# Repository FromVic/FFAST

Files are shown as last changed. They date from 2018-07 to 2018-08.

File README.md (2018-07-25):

# FFAST

## Introduction

The FFAST vehicle is a 1:10 scale RC car functioning as a test platform for testing dynamic motion planning and control algorithms. This repository contains the software developed throughout the project, including the source codes in the vehicle responsible for autonomous driving and executing maneuvers such as drifting and obstacle avoidance.

## Functionalities

The rear-wheel drive front steering vehicle is capable of driving with speed of up to 6 m/s forward and 3 m/s backwards and achieving steering angles of 30 degrees on either side. It achieves localization reasonably well using data from the Hall effect sensors on the motor as odometry, IMU, LIDAR and the camera on the Jetson developer kit with optic flow. It can be teleoperated or controlled by a software giving it navigation commands. An RF receiver on the vehicle stops vehicle operation when the remote transmitter is pressed, acting as an emergency kill switch.

## Organization

The repository is divided into several subfolders:
- doc  
Directory for instructions for developing the RC car platform and the detailed documentation of the project
- catkin_ws  
Catkin workspace containing the ROS packages that control the vehicle
- matlab_simulator  
MATLAB scripts for simulation of vehicle dynamics and execution of the maneuvers in simulation

## Getting Started

The [setup instructions](doc/setup_instructions.md) will get you a copy of the project up and running on your local machine for development and testing purposes. It has been developed for Linux, and no cross-compatibility effort has been made.

## Running the tests
Refer to the [test runs](doc/test_runs.md) for the commands to run the tests.

## Authors

* **Jordan Ford** - [jsford](https://github.com/jsford)
* **Emily Yunan** - [emilyfy](https://github.com/emilyfy)
* **Shihao Xu** - [FromVic](https://github.com/FromVic)

See also the list of [contributors](https://github.com/jsford/FFAST/contributors) who participated in this project.

## License

MIT License  
Copyright (C) 2017 Jordan Ford  
The Robotics Institute, Carnegie Mellon University

Permission is hereby granted, free of charge, to any person obtaining a copy of this software and associated documentation files (the "Software"), to deal in the Software without restriction, including without limitation the rights to use, copy, modify, merge, publish, distribute, sublicense, and/or sell copies of the Software, and to permit persons to whom the Software is furnished to do so, subject to the following conditions: The above copyright notice and this permission notice shall be included in all copies or substantial portions of the Software.

THE SOFTWARE IS PROVIDED "AS IS", WITHOUT WARRANTY OF ANY KIND, EXPRESS OR IMPLIED, INCLUDING BUT NOT LIMITED TO THE WARRANTIES OF MERCHANTABILITY, FITNESS FOR A PARTICULAR PURPOSE AND NONINFRINGEMENT. IN NO EVENT SHALL THE AUTHORS OR COPYRIGHT HOLDERS BE LIABLE FOR ANY CLAIM, DAMAGES OR OTHER LIABILITY, WHETHER IN AN ACTION OF CONTRACT, TORT OR OTHERWISE, ARISING FROM, OUT OF OR IN CONNECTION WITH THE SOFTWARE OR THE USE OR OTHER DEALINGS IN THE SOFTWARE.

## Acknowledgments

* Carnegie Mellon University 
* General Motors Research and Development

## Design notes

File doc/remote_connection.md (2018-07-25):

# Setting up local computer and vehicle remote connections
Other than sharing ROS master, the other steps here are optional but help in speeding up the setup process before test runs. Getting a passwordless sudo is necessary to get the emergency remote kill switch to work. Without a passwordless sudo, the jetson_gpio package will not be able to be run by the ROS server.

## Sharing ROS master
The car and a local computer have to share a common ROS master to run the tests. To do this, they must first be connected to the same network. Then, check the assigned IP on both computers by:
```bash
$ hostname -I
```
Assuming the local computer IP is 10.42.0.1 and the Jetson 10.42.0.2, on the local computer, in every terminal before running the ROS commands run these first
```bash
$ export ROS_MASTER_URI=http://10.42.0.2:11311
$ export ROS_IP=10.42.0.1
```
You can put these lines inside ~/.bashrc to set the ROS master by default. To run your own master, simply reverse the changes:
```bash 
$ export ROS_MASTER_URI=http://localhost:11311
$ unset ROS_IP
```

## Getting passwordless sudo
In the jetson, run the command
```bash
$ sudo visudo
```
On the last line, add the following:
```
username ALL = (ALL) NOPASSWD: ALL
```
replacing username with your user name.  
Note: it is important to use visudo to edit the file instead of manually editing it with other editors as an invalid file will lead to loss of access to sudo privileges.

## Synchronizing time across machines
If the system time in the different machines are not synchronized, the timestamp on ROS messages will differ and this may cause problems. To synchronize the system time, install Chrony on both computers:
```bash
$ sudo apt-get install ntpdate chrony
```
Edit the configuration file `/etc/chrony/chrony.conf` and add the following:  
On the local computer,
```
local stratum 8
allow jetson_ip
```
replacing car_ip with the IP address of the jetson.  
On the Jetson,
```
server local_ip iburst
```
replacing local_ip with the IP address of the local computer.

## Setting up static IP addresses
If a Wi-Fi adapter or router is used specifically for the connection between the local computer and remote RC car, static IP addresses can be assigned to both computers.

Using a Wi-Fi adapter (suppose the static IP to be assigned to the car is 10.42.0.2):
1. Connect the USB adapter to the local computer
2. Create a new Wi-Fi network , choosing the corresponding Wi-Fi adapter.
3. On the IPv4 settings, select the dropdown for Method to be Shared to other computers;In the Wi-Fi tab set Mode to 'Ad-hoc'         and Band to 'B/G (2.4 GHz)'.
4. On the Jetson, connect to the created Wi-Fi network.
5. Edit the network connection such that:  
   In the general tab both 'Automatically connect to this network when it is available' and 'All users may connect to this network' are checked  
   In the Wi-Fi tab set Mode to 'Ad-hoc' and Band to 'B/G (2.4 GHz)'
   In the IPv4 Settings tab the Method is set to Manual and add an address with  
   Address: 10.42.0.2  
   Netmask: 24  
   Gateway: 10.42.0.1 (IP of host)  
   DNS Servers: 8.8.8.8, 8.8.4.4
6. Disconnect and connect to the network again.

## Setup SSH shortcut
To avoid having to type in `ssh username@hostname` or `ssh username@hostip` everytime to access the remote terminal, one can setup an SSH config file to to create a shortcut for SSH to the host. (Instructions obtained from [here](http://nerderati.com/2011/03/17/simplify-your-life-with-an-ssh-config-file/)).
```bash
$ nano ~/.ssh/config
```
Enter the following:
```
Host shortcutname
HostName hostname
Port portnumber
User username
```
with the corresponding shortcut name, host name, port number and username. The default port number is 22.  
Then,
```bash
$ cd /etc/bash_completion.d/
$ sudo nano ssh
```
Copy and paste the following:
```
_ssh() 
{
    local cur prev opts
    COMPREPLY=()
    cur="${COMP_WORDS[COMP_CWORD]}"
    prev="${COMP_WORDS[COMP_CWORD-1]}"
    opts=$(grep '^Host' ~/.ssh/config | grep -v '[?*]' | cut -d ' ' -f 2-)

    COMPREPLY=( $(compgen -W "$opts" -- ${cur}) )
    return 0
}
complete -F _ssh ssh
```
From here onwards, the command `ssh shortcutname` will be equivalent to entering `ssh username@hostname -p portnumber`.

## Setting RSA key
Another inconvenience when accessing remote terminal is the need to enter the password everytime. However, by setting up the RSA key one can eliminate the need to do so. While connected to the same network, on the local computer:
```bash
$ ssh-keygen
  press enter or type your preferred file name for storing the key  
  press enter or type a password (this is a password to bet set on the stored key, not the user account password)  
  press enter again or type the same password  
$ chmod 755 ~/.ssh
$ ssh-copy-id -i id_rsa user@hostname (or change id_rsa to the filename you entered)
$ ssh -oHostKeyAlgorithms='ssh-rsa' user@hostname (if it fails, change ssh-rsa to the type shown in ~/.ssh/known_hosts)
$ chmod 600 ~/.ssh/authorized_keys
$ exit exit
$ ssh-agent bash
$ ssh-add ~/.ssh/id_rsa (or change id_rsa to the filename you entered)
$ exit
```
This needs to be done only the first time you use SSH to access the Jetson terminal. After this you can simply use the `ssh user@hostname` command

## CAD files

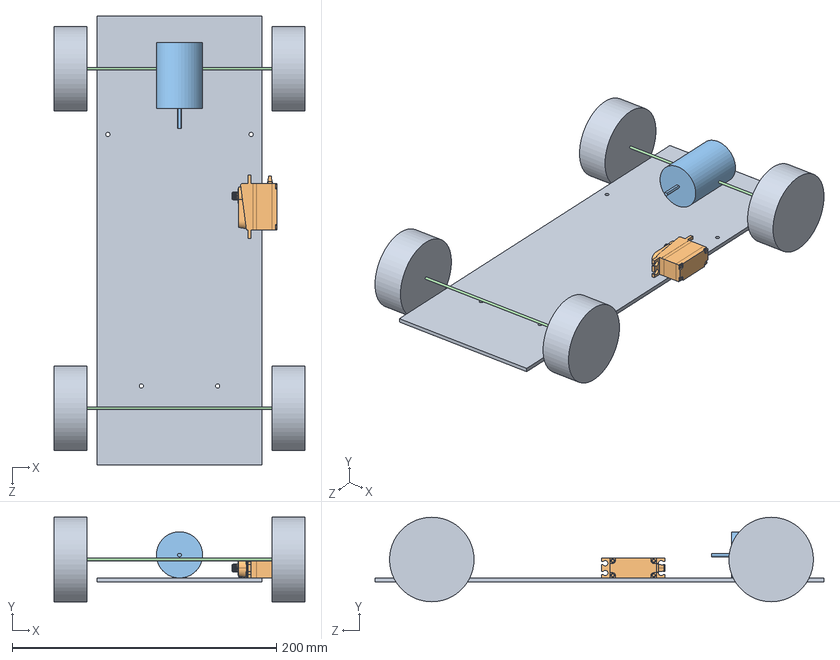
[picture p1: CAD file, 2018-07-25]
doc/CAD files/chassis with drivetrain.SLDASM
190.0 x 64.0 x 340.0 mm
chassis
Savox
motor
axle x 2

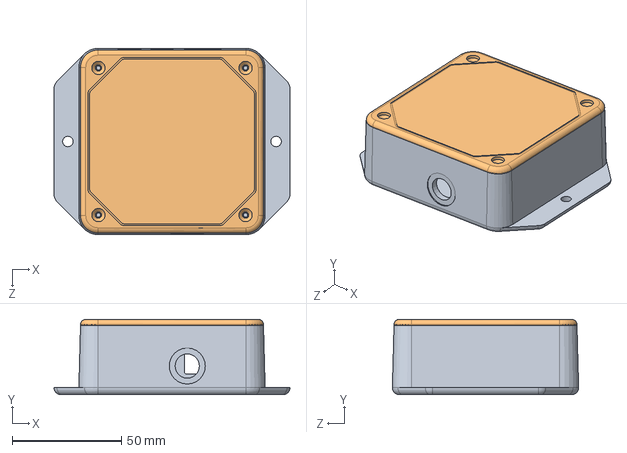
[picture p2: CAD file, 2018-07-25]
doc/CAD files/velodyne interface box.SLDASM
108.0 x 34.5 x 85.2 mm
50-6001a FAB ENCLOSURE
50-6002a LID ENCLOSURE

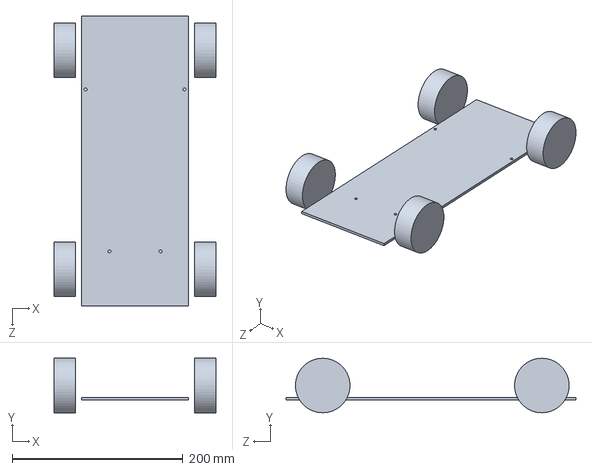
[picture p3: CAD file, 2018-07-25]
doc/CAD files/chassis.SLDPRT
190.0 x 64.0 x 340.0 mm

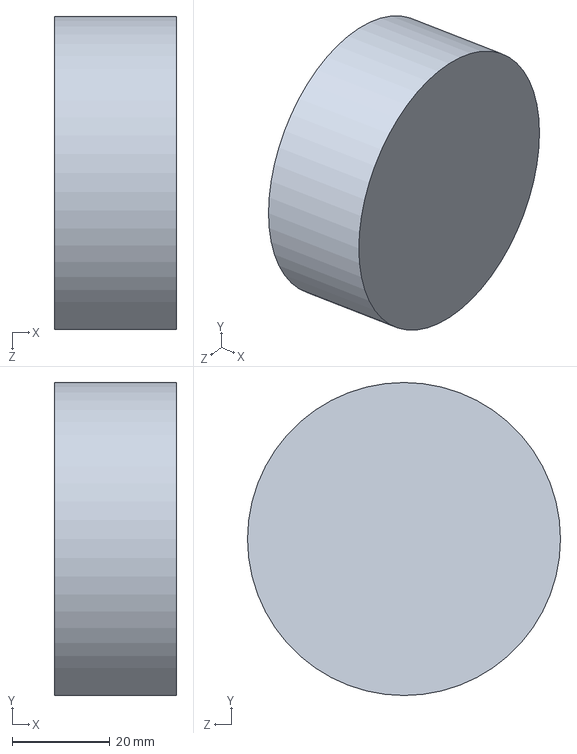
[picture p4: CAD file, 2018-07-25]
doc/CAD files/wheel.SLDPRT
25.0 x 64.0 x 64.0 mm

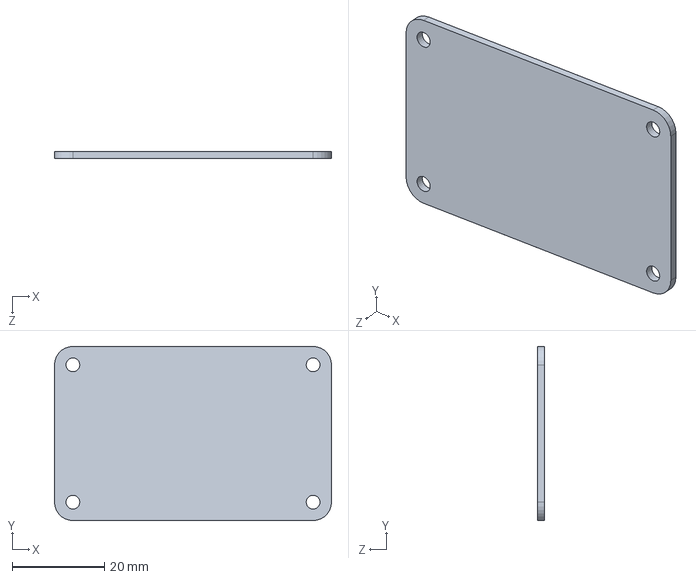
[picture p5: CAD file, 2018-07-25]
doc/CAD files/Vreg.SLDPRT
60.2 x 37.8 x 1.50 mm

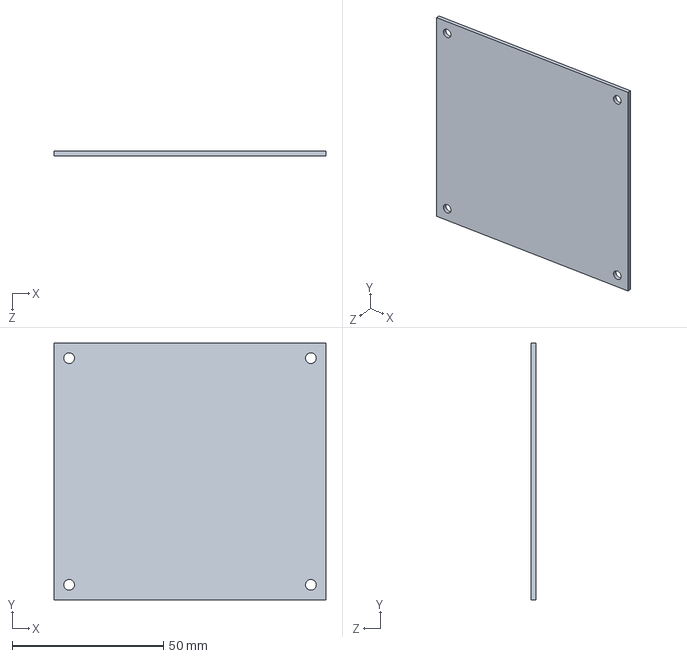
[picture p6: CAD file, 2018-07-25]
doc/CAD files/power dist board.SLDPRT
90.0 x 85.0 x 1.50 mm

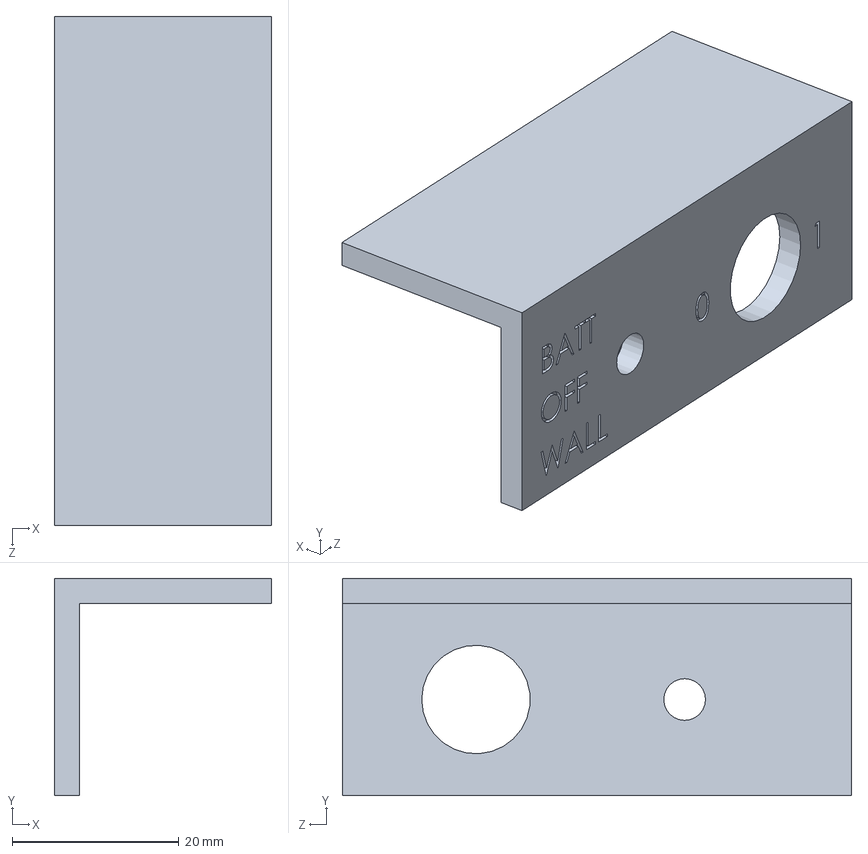
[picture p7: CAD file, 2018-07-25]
doc/CAD files/switch mount.SLDPRT
26.0 x 26.0 x 61.0 mm

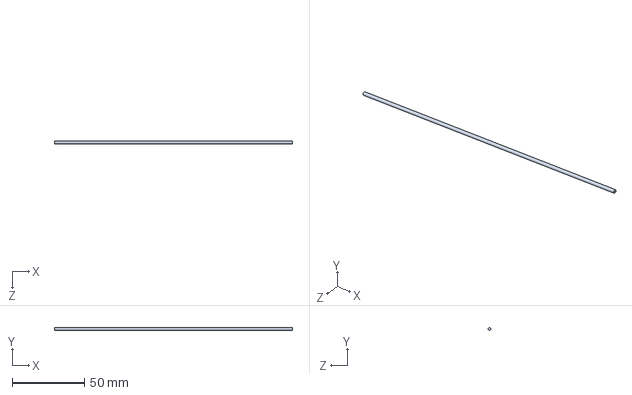
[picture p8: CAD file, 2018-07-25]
doc/CAD files/axle.SLDPRT
165.0 x 2.00 x 2.00 mm

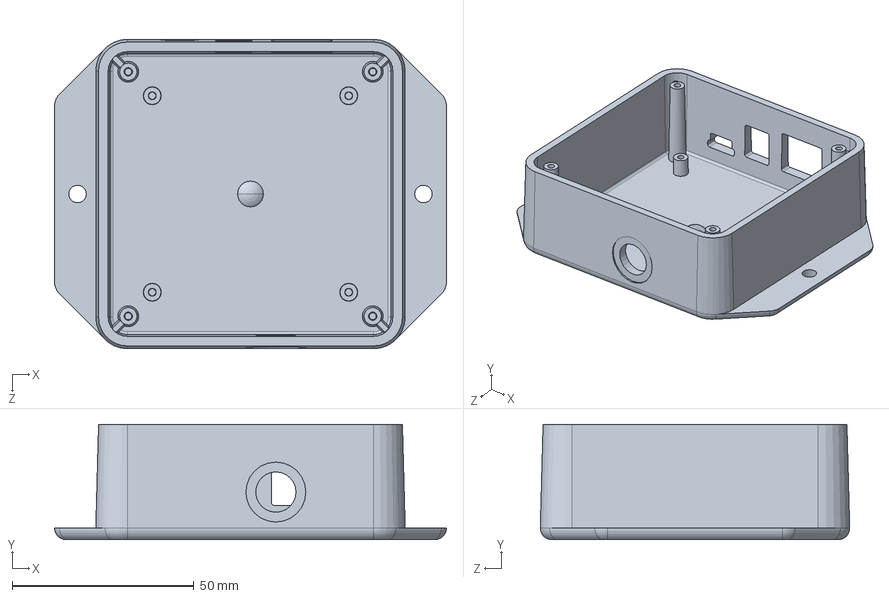
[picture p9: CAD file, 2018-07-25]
doc/CAD files/50-6001a FAB ENCLOSURE.SLDPRT
108.0 x 31.8 x 85.2 mm

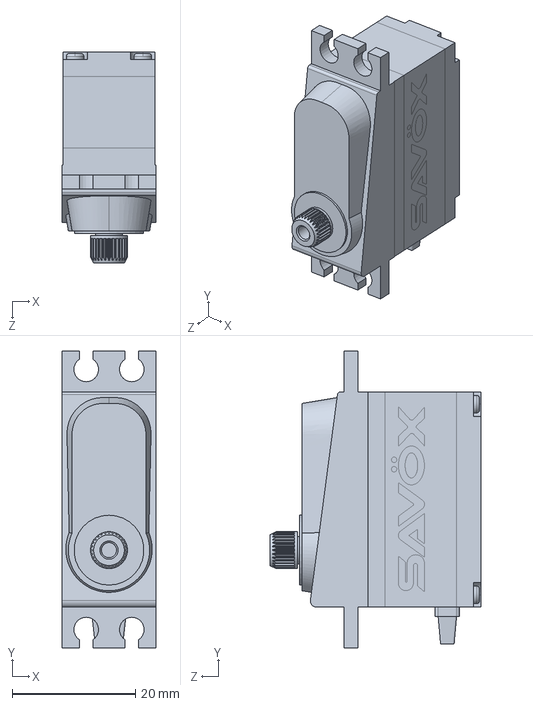
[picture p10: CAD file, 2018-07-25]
doc/CAD files/Savox.SLDPRT
15.2 x 48.2 x 34.3 mm

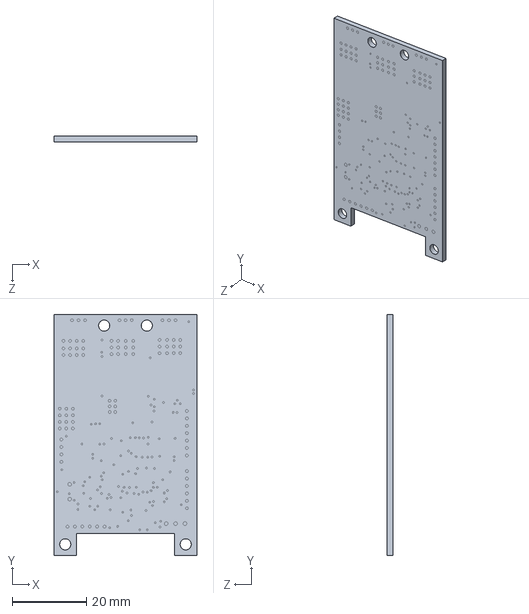
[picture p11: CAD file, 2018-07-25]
doc/CAD files/vesc.SLDPRT
38.5 x 65.0 x 1.58 mm

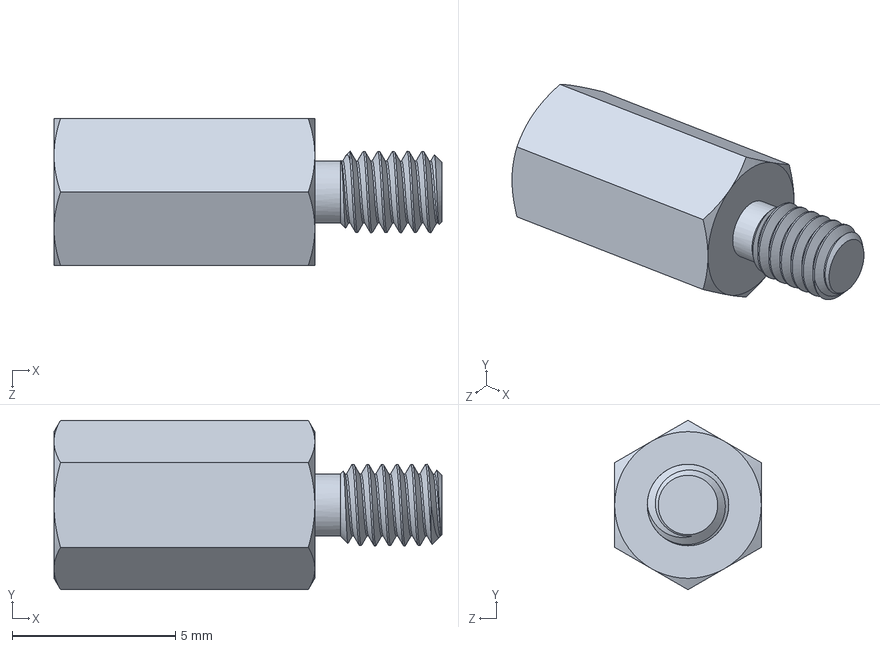
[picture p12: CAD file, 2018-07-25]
doc/CAD files/M2.5 8mm Male-Fem Standoff.SLDPRT
11.9 x 5.20 x 4.50 mm

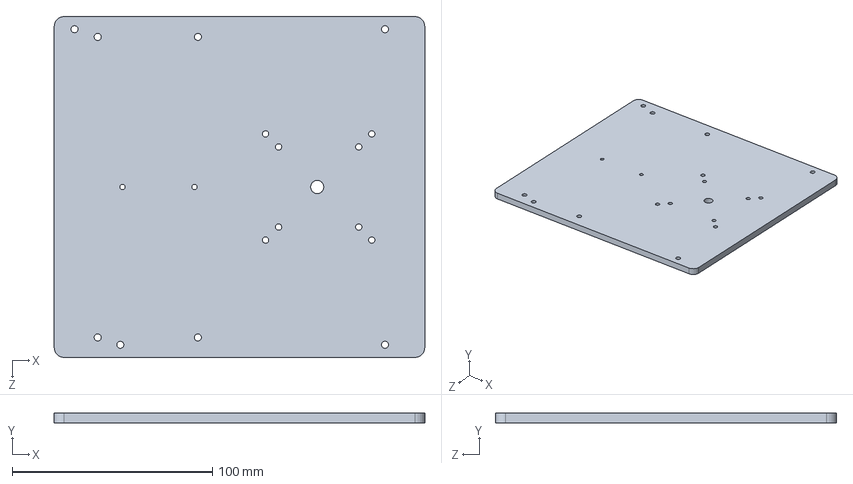
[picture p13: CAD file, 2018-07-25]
doc/CAD files/top plate.SLDPRT
185.0 x 4.76 x 170.2 mm

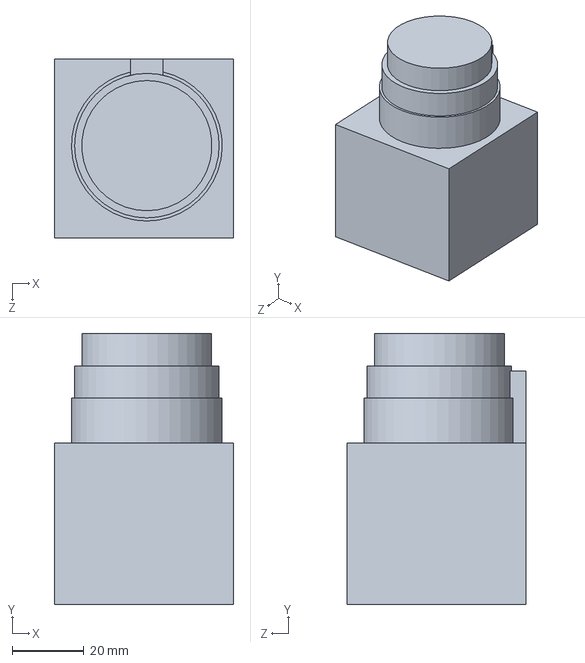
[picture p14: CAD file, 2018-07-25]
doc/CAD files/Hokuyo URG-04LX-UG01.SLDPRT
50.0 x 75.5 x 50.0 mm

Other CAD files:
doc/CAD files/6-32 2.5in Fem Standoff.SLDPRT
doc/CAD files/battery.SLDPRT
doc/CAD files/motor.SLDPRT
doc/CAD files/bottom plate.SLDPRT
doc/CAD files/50-6002a LID ENCLOSURE.SLDPRT
doc/CAD files/6-32 .25in Fem Standoff.SLDPRT
doc/CAD files/6-32 1in Male-Fem Standoff.SLDPRT
doc/CAD files/91115a134_18-8 ss fem thrded hex standoff.SLDPRT
doc/CAD files/91780A123_ALUM FEM THRDED HEX STANDOFF.SLDPRT
doc/CAD files/91780A133_ALUM FEM THRDED HEX STANDOFF.SLDPRT
doc/CAD files/93505A440_ALUM MALE-FEM THRDED HEX STANDOFF.SLDPRT
doc/CAD files/95783A019_NYLON 6-6 MALE-FEM THRDED HEX STANDOFF.SLDPRT
doc/CAD files/IMU.SLDPRT
doc/CAD files/Top cover.SLDPRT
doc/CAD files/big toggle switch.SLDPRT
doc/CAD files/protoboard.SLDPRT
doc/CAD files/small toggle switch.SLDPRT
doc/CAD files/usb hub.SLDPRT
doc/CAD files/velodyne lidar.SLDPRT
doc/dxf files/Top cover.DXF
doc/dxf files/top plate.DXF

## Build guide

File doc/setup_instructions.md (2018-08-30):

# Setup Instructions

## Parts List
| Component | Manufacturer & Model no. |
| ---|---|
| RC car chassis & drivetrain | MST FXX-D |
| Sensored BLDC motor | MST XBLS 601012 |
| Pinion gear | Boom racing 48P 19T |
| Servo motor | Savox SAVSB2274SG |
| Battery | Multistar 3S 11.1V 5200mAh |
| Single-board computer | Nvidia Jetson TX2 |
| IMU | Variense VMU931 |
| LIDAR | Hokuyo URG-04LX-UG01 |
| ESC | VESC 4.12 |

Other parts required include:
- acrylic plates
- switches
- gamepad controller
- USB hub
- USB to micro USB (x1) and USB to mini USB (x2) cables
- USB Wi-Fi adapter (optional)
- Wireless switch transmitter and receiver (for emergency remote kill switch, optional)
- PCB and components
- fasteners and standoffs
- wires and connectors

Refer to the [bill of materials](bill\ of\ materials.xlsx) for the complete list and websites the parts were sourced from in our project.

## Steps
1. Laser cut the acrylic plates with the DXF files in doc folder.
2. Manufacture the PCB with the eagle and gerber files.
3. Setup the electrical connections according to the [circuit diagram](circuit_diagram.pdf).
4. Load the firmware into the VESC and calibrate its settings (instructions [here](vesc_setup.md)).
5. Assemble the car according to the 3D mechanical design of the vehicle from [here](FFAST_Assem.SLDASM).
6. [Install ROS](http://wiki.ros.org/kinetic/Installation/Ubuntu) and all other [package dependencies](dependencies.md) on the Jetson TX2.(Please make sure the ROS verison installed to be ROS kinetic, otherwise there might be some compatibility problems)
7. Set the udev rules on the Jetson (for the VESC, IMU and LIDAR) and the local computer (for the controller). Refer to the [rules file](99-usb-serial.rules) and use the same symbolic links, changing the values accordingly. (Joystick settings may vary due to different types of controllers, please check values)
8. Have a local computer with ROS and the same packages installed to remotely control the car.
9. Setup the network connections between the local computer and the car (instructions [here](remote_connection.md)).
10. The vehicle is now ready for [test runs](test_runs.md).

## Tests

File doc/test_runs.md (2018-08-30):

# Test Runs
To power up the car, plug battery into voltage input plug on the power distribution board, and press the VESC switch button beside it. Once the blue light on VESC is turned on, press power button of the Jestson then the whole system will be turned on.

After powering up the Jetson and the VESC with the on-board battery and setting up the necessary remote network connections, the car is ready for running.

## Fundamental launches
```bash
$ roslaunch hardware hardware.launch
```
This starts all the hardware operations, including the VESC, IMU, LIDAR, camera, the corresponding static transforms broadcaster and the emergency kill switch listener on the GPIO. At this point, only odometry data and transform is published.  
The launch arguments are:
- predict_slip  
  Set to true to predict wheel slip. Displacement is underestimated during acceleration and high speed and overestimated during deceleration or braking.
- fuse_odom  
  Set to true to fuse the IMU data with motor sensors data before publishing in odom frame. The yaw will then always be obtained from the IMU.
- odom_tf  
  Set to true to broadcast odom to base_link transform.
```bash
$ roslaunch localization localization.launch
```
This starts the localization process, including scan matching, optic flow calculation, particle filter localization within the map and EKF that fuses all these data and output the final pose estimate.
The launch arguments are:
- fuse_odom  
  Same argument needs to be passed as the one to hardware.launch.
- use_scan_matcher  
  Set to true to perform scan matching on LIDAR scans and include the output in the EKF.
- use_amcl  
  Set to true to perform particle filter localization on the LIDAR scans and include the output in the EKF. If true, a map must be provided.
- map  
  The name of the map. The map files (pgm and yaml) must be placed inside the map folder inside the ffast package. Please make sure cartain map is used when localization is launched, it would influence the result of test.

## Teleoperation of the car
In the local computer with a controller connected,
```bash
$ roslaunch user_interface joy.launch
```
Refer to the [schematic](controller.jpg) for details.

## Navigation to Goal
```bash
$ roslaunch ffast ffast.launch
```
This command will launch hardware, localiztion and planning at the same time.

Or you can launch them step by step to check status of each part.
```bash
$ roslaunch hardware hardware.launch
$ roslaunch localization localization.launch
$ roslaunch planning move_base.launch
```
Setting the goal on rviz will command the car to navigate towards the goal.

## Evasive Maneuver
After launching the hardware and localization files, the evasive maneuver can be run with
```bash
$ roslaunch planning evasive_maneuver.launch
```
This by default sets the car to run towards a goal 5 m ahead.
Launch arguments:
- obs_detect  
  Set to true to detect the presence of obstacles from the LIDAR scans. When false, virtual obstacles are introduced.
- obs_speed  
  Set to the speed of the obstacle (from 1 to 4, in m/s). Value of 5 introduces multiple obstacles one after another.

## Drift Cornering
Note that this maneuver has not been successfully performed yet.  
The drift cornering maneuver can similarly be run after launching the hardware and localization files with
```bash
$ roslaunch planning drift_cornering.launch
```
